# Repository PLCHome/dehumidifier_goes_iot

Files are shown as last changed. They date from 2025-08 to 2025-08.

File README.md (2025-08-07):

# My dehumidifier becomes an IoT device

**Please note that opening electrical devices is life-threatening! Opening electrical devices and working on them requires training and authorization.**

**Never work on devices connected to the electrical grid, regardless of whether they are turned on or off.**

**If you follow or replicate parts of this description, you do so entirely at your own risk. I am not liable for any damage caused, including damage to your health and life.**

### Introduction

I've had this TROTEC TTK70 device for many years. It helps me keep my basement dry in the summer.
You can, of course, turn the dehumidifier on every day and let it run for a few hours.
My problem is that I want to use the power from the PV system for this. However, since I leave the house at 6:30 a.m., it doesn't generate enough electricity, depending on the time of year.
At first, I considered using a timer. But this device only beeps once and then stops working when the power comes back on.

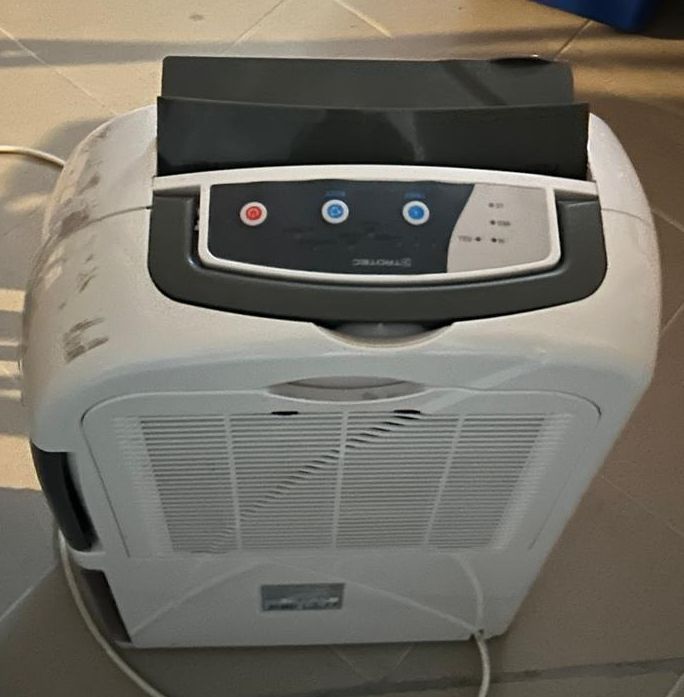
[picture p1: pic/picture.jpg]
Device


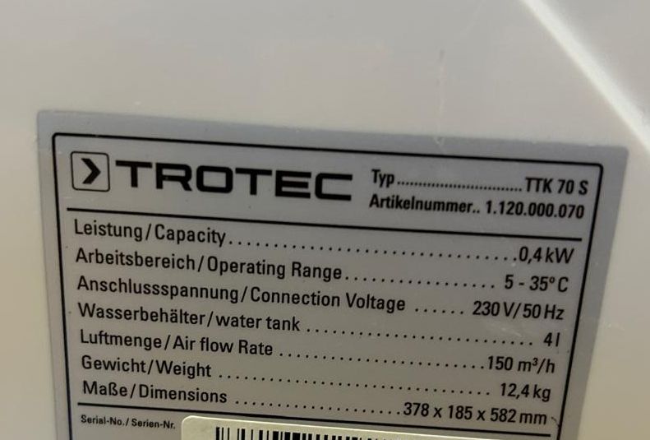
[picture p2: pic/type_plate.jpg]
type plate


## Implementation

**Working with electricity is your own responsibility. I am not liable for any damage, including damage to your health.**

Since the circuit diagram attached to the side was also not informative

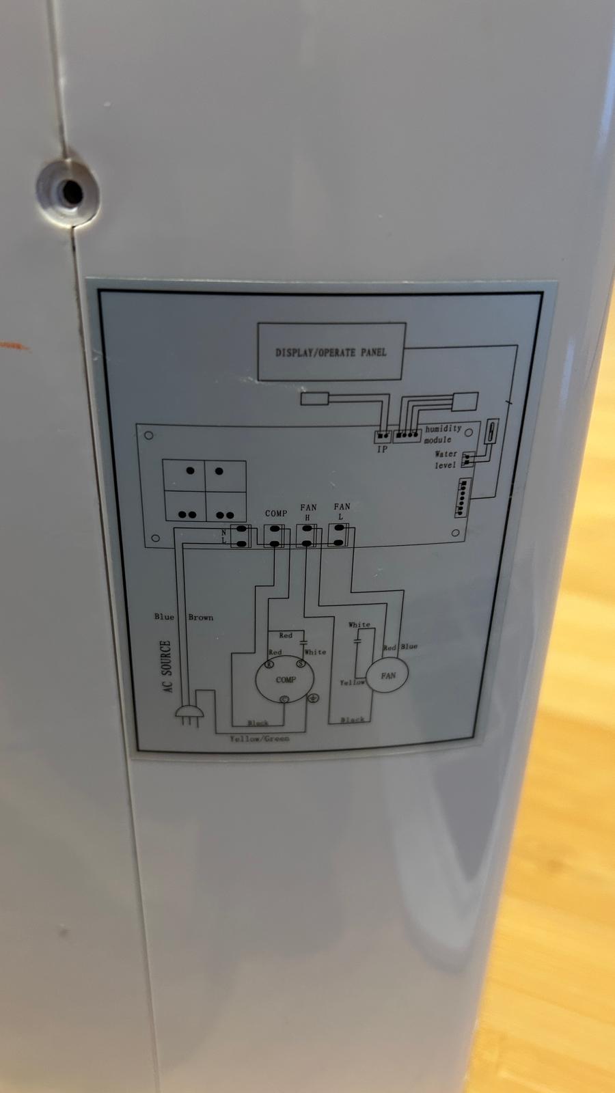
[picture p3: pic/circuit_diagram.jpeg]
circuit diagram


I took a look at the device from the inside and noticed that there was a control panel. I drew its circuit diagram and considered how it might work.

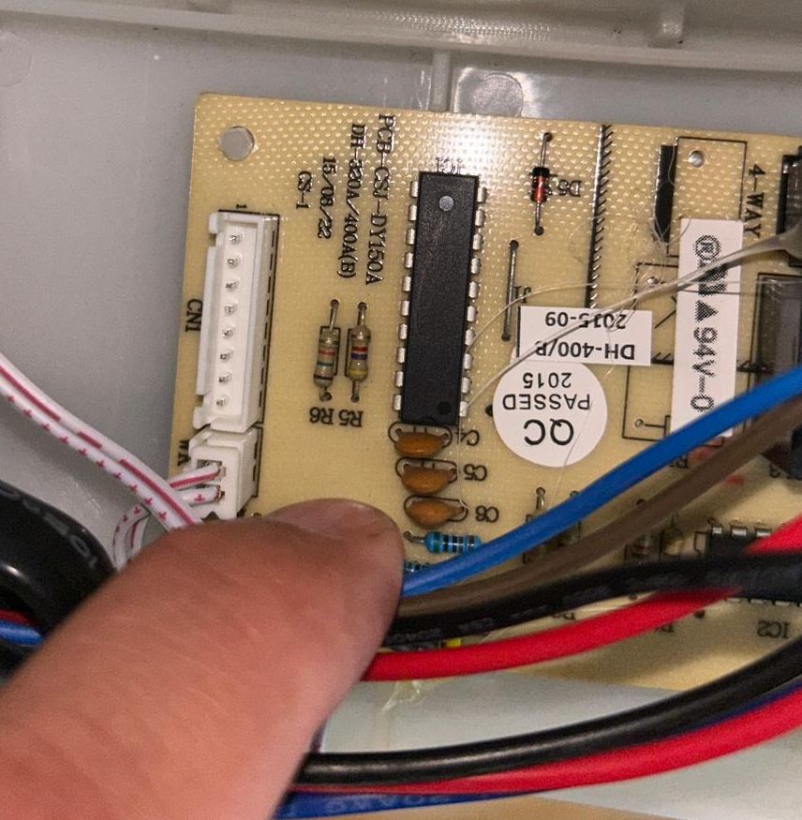
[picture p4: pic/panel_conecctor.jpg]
panel connector


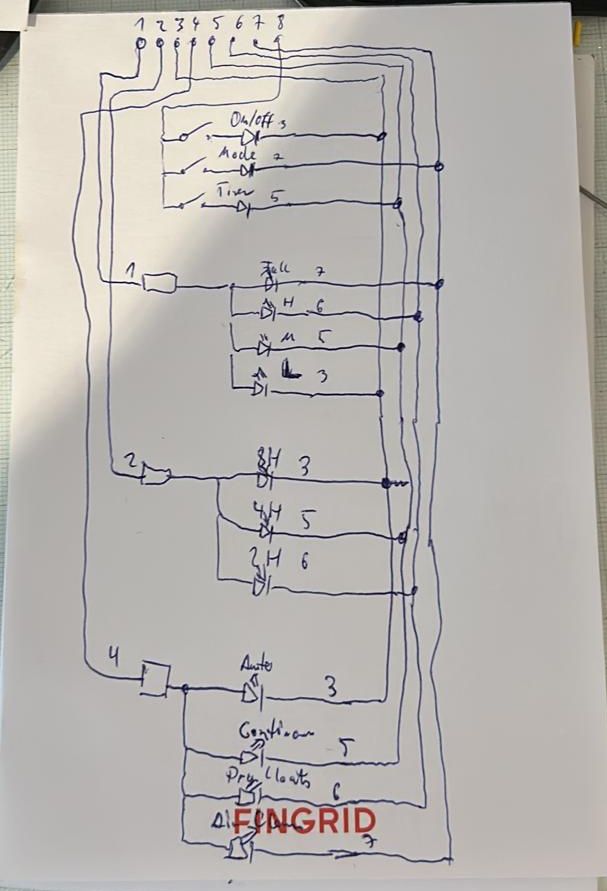
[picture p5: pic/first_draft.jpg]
first draft


The connector has 8 contacts. You can see from the diodes that 1, 2, and 4 are positive, and 3, 5, 6, and 7 are negative.

Since not all LEDs light up at the same time, there must be a control system behind them. I figured that the microcontroller in the device connects lines 3, 5, 6, and 7 to negative one after the other and turns on lines 1, 2, and 4 at the right moment to turn on the LED. We'll refer to lines 3, 5, 6, and 7 as rotating lines.

That leaves the three buttons and line 8. The diodes are there to prevent the wrong LEDs from lighting up when two buttons are pressed at once. And the function is also somewhat instructive. If you pull line eight high with a pull-up resistor, it goes low when the connected rotating line goes negative and the button is pressed.

The only remaining issue is the power supply. However, since the dehumidifier has a transformer built in that always supplies 12V AC when plugged in, that was quickly resolved. Just connect two wires to the output of the rectifier circuit; that's it.

second one

So I gathered a few parts from my stash and started experimenting on the bash board.

I quickly decided to try it with ESPHome and an ESP32-S3 mini that was lying on my desk.

The main problem with the dehumidifier is a microcontroller connected to an LS7805. The ESP32 only requires 3.3V on the GPIOs. If I connect the ESP32 to the same ground via the voltage converter and place the data lines on 3.3V pull-up resistors like the manufacturer did with the buttons, it should work. I didn't even need to solder the pull-ups. They're already built into the ESP32. While lengthening the pins, I noticed that I have two ESP32s that are identical in size but not identical. I have an ESP32-S3 mini and an ESP32-S3 tiny. It's important to note that GPIO 3 is in a different location on both. Since there are boot issues with this GPIO, you shouldn't use GPIO 3. Furthermore, the ESP32-S3 tiny must be installed upside down. Since an ESP32 connected to a 3.3V supply died in another project, I'm now only using 5V voltage converters. However, it seems to be recommended that the ESP generate the 3.3V itself.

Simple transistors should be sufficient for the buttons. Since I don't know the breakdown voltages, I preferred to use diodes there.

Oh, the diodes don't really matter, just like the transistors. I had a large pile of them in stock here. But any other NPN transistor or any other diode will work.

I didn't feel like drawing the ESP, and I couldn't find a finished one. So I just used two connectors.

iot circuit

A friend was kind enough to mill a circuit board for me on his CNC milling machine. It looks a bit better than a perforated board.

iot pcb

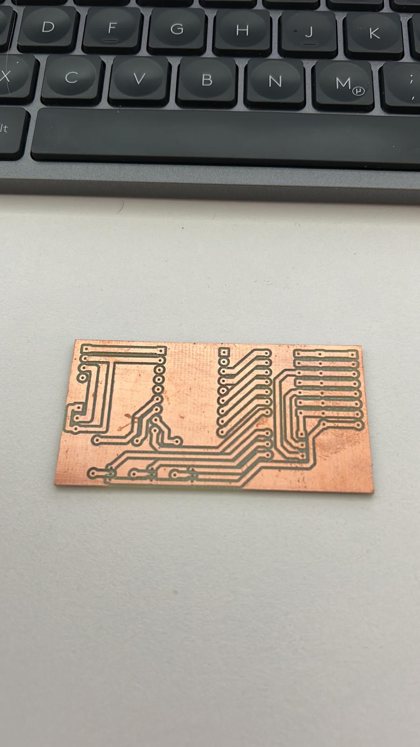
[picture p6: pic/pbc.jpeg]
pbc


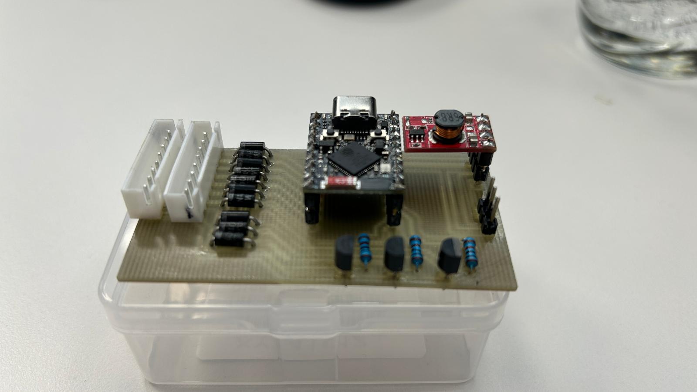
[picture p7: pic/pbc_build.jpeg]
pbc build up


After inserting the board into the device, the ESP32 rebooted every time I turned the device on and off. This wasn't good. I then used the other controller from Waveshare. This one also requires upside-down installation and has a different GPIO order. I adjusted the layout so that it now works with both. I modified the underside of the board. The dead copper surface was quite useful here. It works with this one. I also added the capacitor to the board because I was trying to use it to prevent the mini ESP32 from booting. But it seems to be the proximity to the relays and not the supply voltage. The capacitor is 2200uF and is connected to the 5V line to the controller.

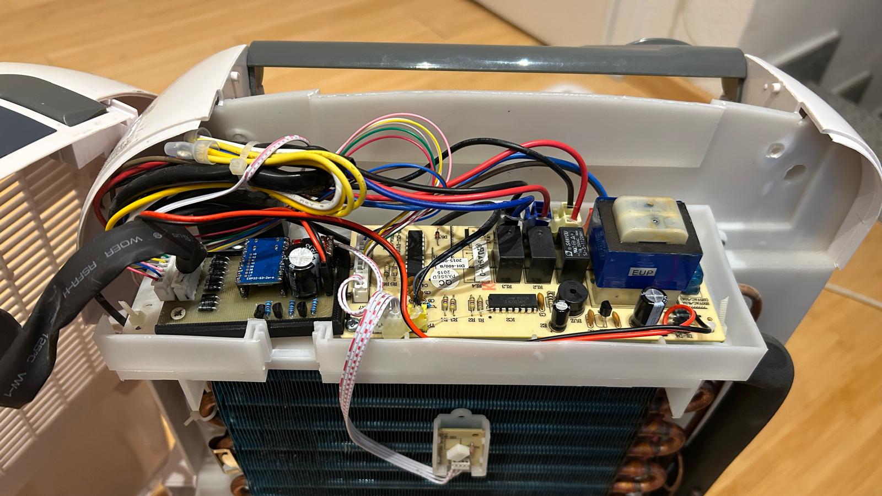
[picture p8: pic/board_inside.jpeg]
board inside


## ESPHome and the homeassist

And then the YAML for ESP Home, and here it is in Home Assistant. You can select one of the four modes and OFF using the top selection. The one below allows you to select the integrated timers 2H, 4H, 8H, and OFF. After the controller has selected the setting, it resets to "–" which means nothing is selected there. The states are displayed below as text sensors. There are also two binary sensors for on and water tank full.

When you select a mode, the ESP first checks whether the device is on or off and presses the power button if necessary. The ESP32 then presses the mode button repeatedly until the correct mode is selected.

For the timer, it presses the timer button repeatedly until the selection is made.

Press a button? Not really, it controls the transistors, but to the microcontroller in the dehumidifier, it looks like a button press...

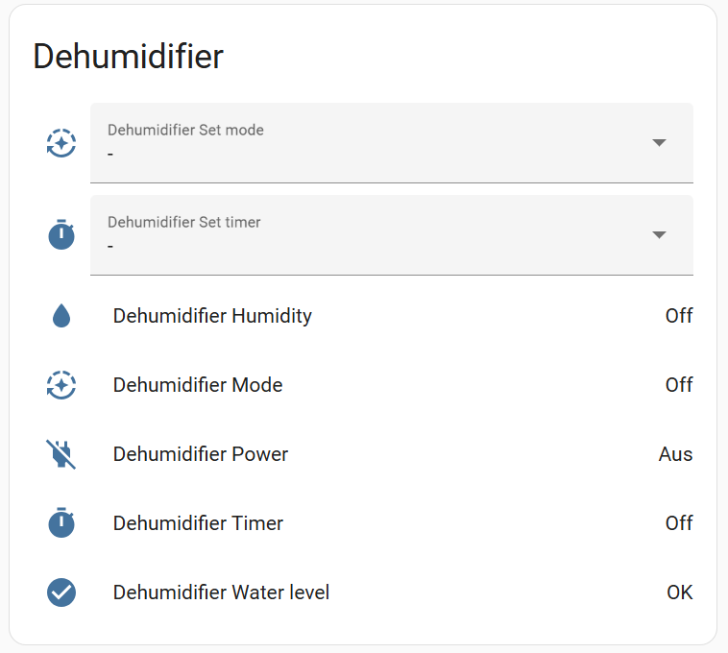
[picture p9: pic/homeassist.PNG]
homeassist


**Working with electricity is your own responsibility. I am not liable for any damage, including damage to your health.**

Do you have such great projects? Write me...

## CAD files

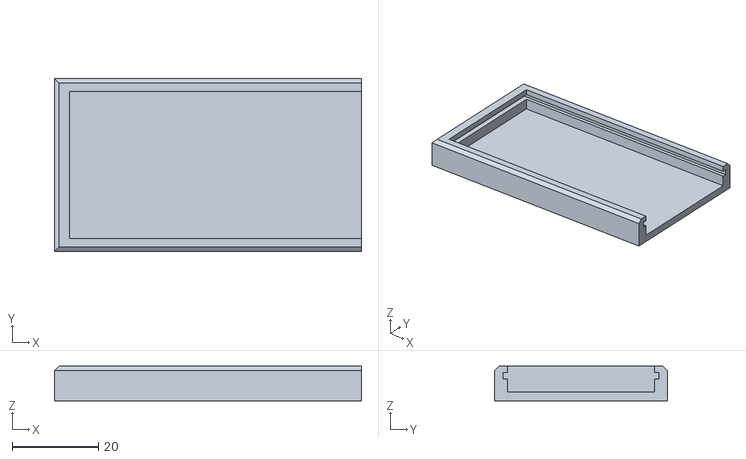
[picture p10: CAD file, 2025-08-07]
FreeCad/Platinenhalter-Body.stl
71.0 x 40.0 x 8.00

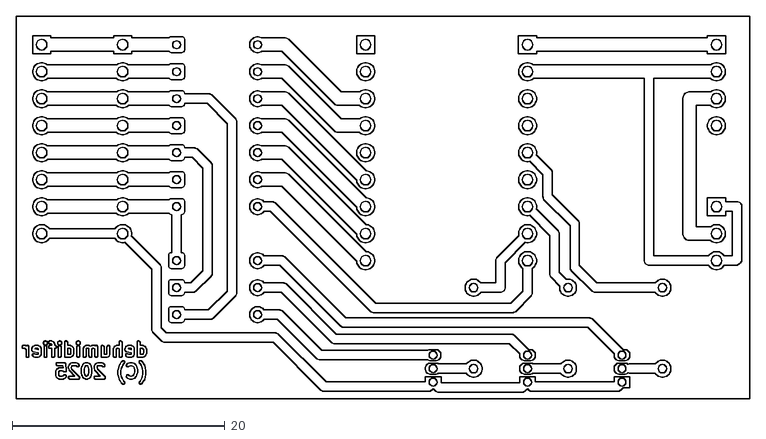
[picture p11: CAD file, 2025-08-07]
KICad/dehumidifier/export/dehumidifier-B_Cu.dxf
69.0 x 36.0

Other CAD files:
FreeCad/Platinenhalter.FCStd

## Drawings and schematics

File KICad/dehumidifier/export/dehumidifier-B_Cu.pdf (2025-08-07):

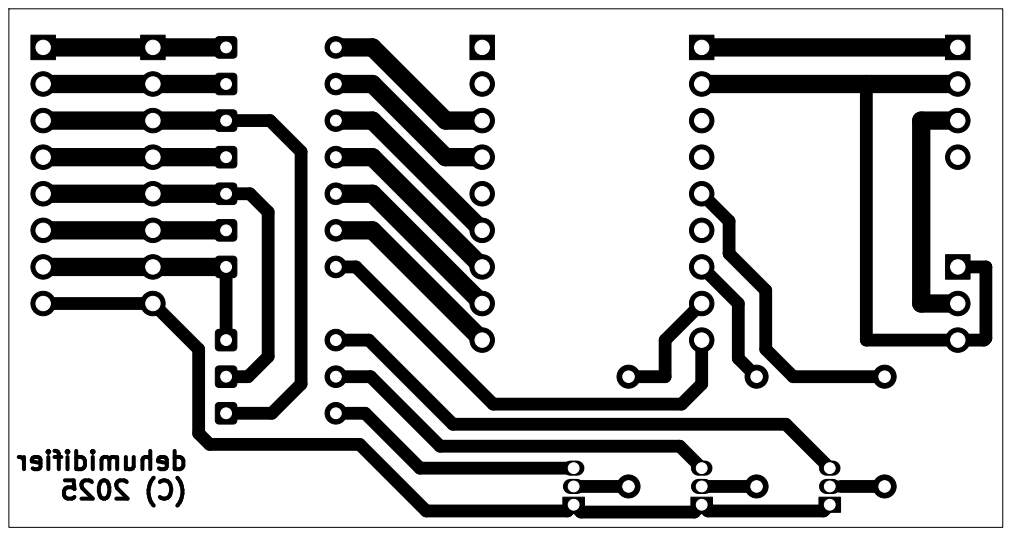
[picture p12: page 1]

Id: 1/1 Title: File: dehumidifier.kicad_pcb Sheet:

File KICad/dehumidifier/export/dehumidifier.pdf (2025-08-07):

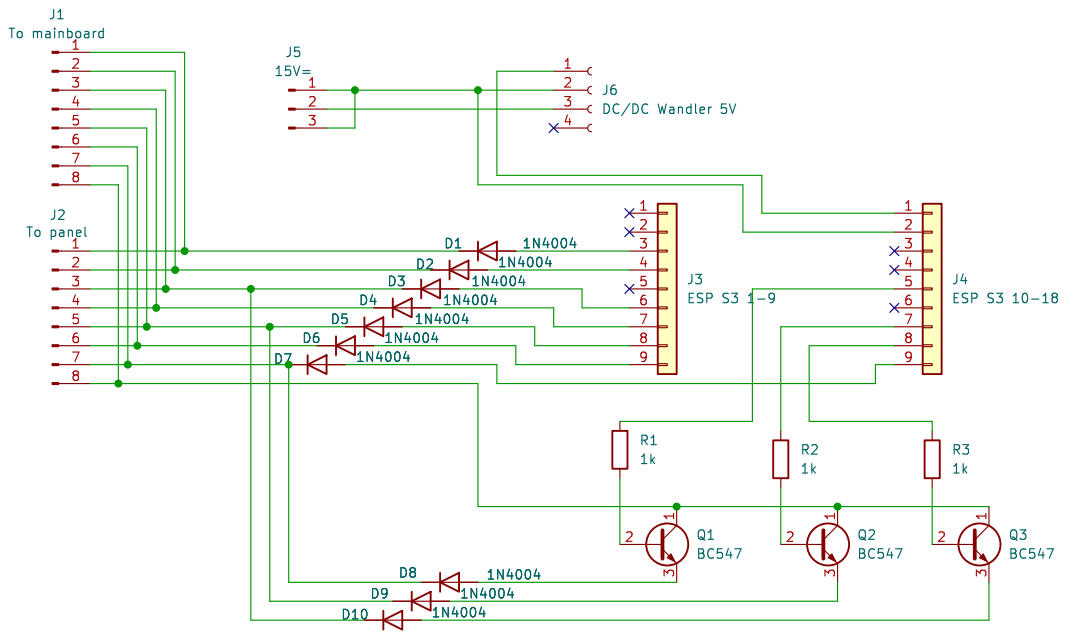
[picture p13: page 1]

Id: 1/1 Title: File: dehumidifier.kicad_sch Sheet: /

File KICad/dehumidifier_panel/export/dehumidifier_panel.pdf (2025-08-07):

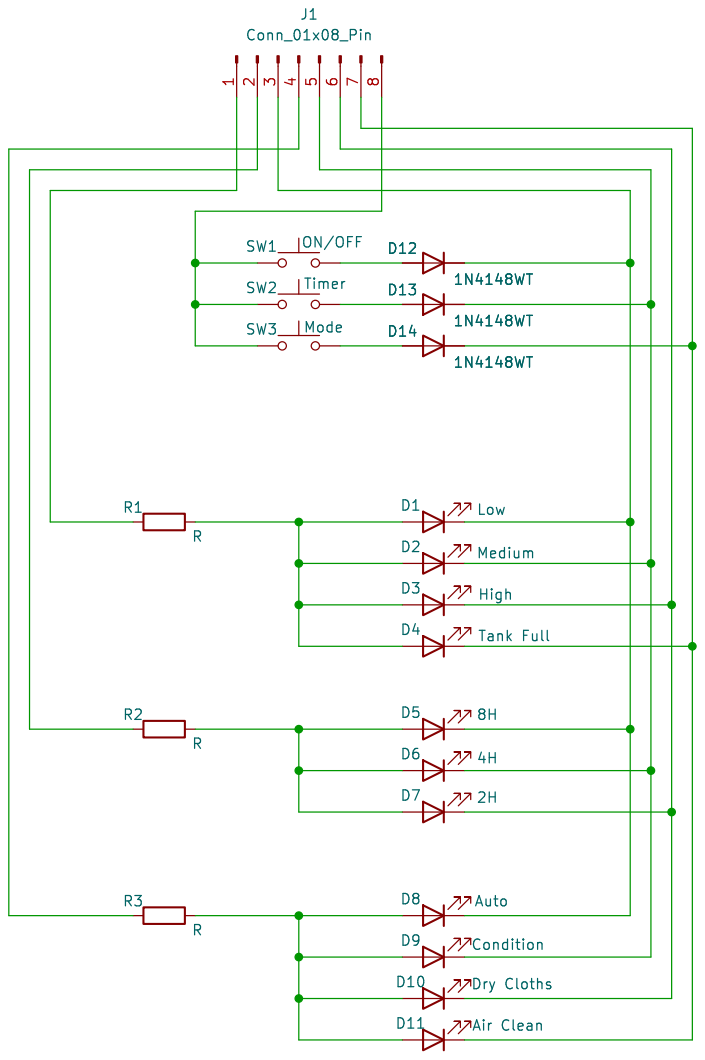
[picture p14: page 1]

Id: 1/1 Title: File: dehumidifier_panel.kicad_sch Sheet: /

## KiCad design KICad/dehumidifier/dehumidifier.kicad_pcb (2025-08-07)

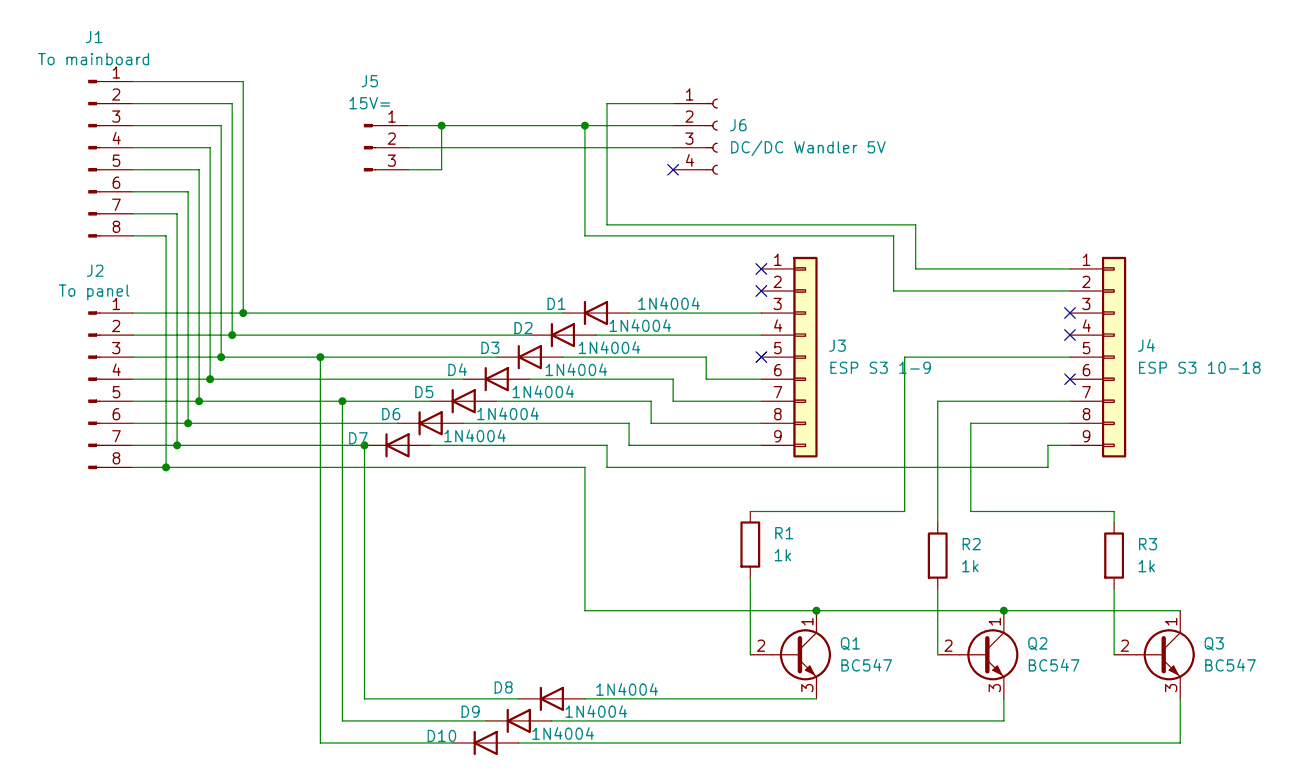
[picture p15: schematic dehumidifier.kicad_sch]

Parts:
D1, D2, D3, D4, D5, D6, D7, D8, D9, D10: 1N4004; D_DO-34_SOD68_P7.62mm_Horizontal
J1: To mainboard; PinHeader_1x08_P2.54mm_Vertical
J2: To panel; PinHeader_1x08_P2.54mm_Vertical
J3: ESP S3 1-9; PinHeader_1x09_P2.54mm_Vertical
J4: ESP S3 10-18; PinHeader_1x09_P2.54mm_Vertical
J5: 15V=; PinHeader_1x03_P2.54mm_Vertical
J6: DC/DC Wandler 5V; PinHeader_1x04_P2.54mm_Vertical
Q1, Q2, Q3: BC547; TO-92_Inline
R1, R2, R3: 1k; R_Axial_DIN0207_L6.3mm_D2.5mm_P7.62mm_Horizontal

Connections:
unnamed: D1.2 (A), J3.3
unnamed: D1.1 (K), J1.1, J2.1
unnamed: D2.2 (A), J3.4
unnamed: D2.1 (K), J1.2, J2.2
unnamed: D3.2 (A), J3.6
unnamed: D4.2 (A), J3.7
unnamed: D4.1 (K), J1.4, J2.4
unnamed: D5.2 (A), J3.8
unnamed: D5.1 (K), D9.1 (K), J1.5, J2.5
unnamed: D6.2 (A), J3.9
unnamed: D6.1 (K), J1.6, J2.6
unnamed: D7.2 (A), J4.9
unnamed: D7.1 (K), D8.1 (K), J1.7, J2.7
unnamed: D8.2 (A), Q1.3 (E)
unnamed: D9.2 (A), Q2.3 (E)
unnamed: D10.2 (A), Q3.3 (E)
unnamed: D3.1 (K), D10.1 (K), J1.3, J2.3
unnamed: J1.8, J2.8, Q1.1 (C), Q2.1 (C), Q3.1 (C)
unnamed: J4.1, J6.1
unnamed: J4.2, J5.1, J5.3, J6.2
unnamed: J4.5, R1.1
unnamed: J4.7, R2.1
unnamed: J4.8, R3.1
unnamed: J5.2, J6.3
unnamed: Q1.2 (B), R1.2
unnamed: Q2.2 (B), R2.2
unnamed: Q3.2 (B), R3.2

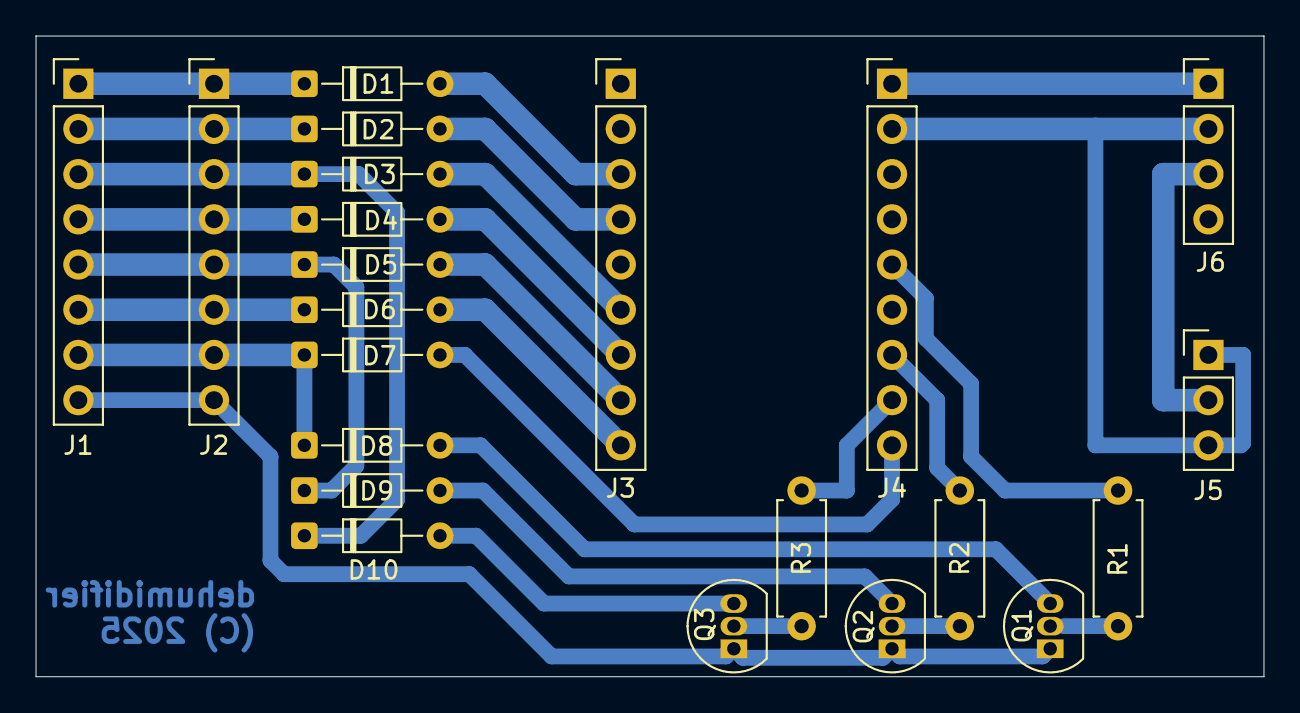
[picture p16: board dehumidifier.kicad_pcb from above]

Board: 2 copper layers, 69.0 x 36.0 mm, 22 parts (0 on the bottom side), 27 nets.

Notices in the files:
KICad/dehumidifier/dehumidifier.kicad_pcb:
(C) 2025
